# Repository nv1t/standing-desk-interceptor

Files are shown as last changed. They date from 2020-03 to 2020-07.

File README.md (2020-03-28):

# standing-desk-interceptor
I wanted to intercept the communication between my Flexispot E5B standing desk buttons. This is the progress on the project.
It should work on any other flexispot desk as well, as i suspect they use the same button interface with nearly the same protocol. But this needs testing!

# RJ45 Pins
```
1 - RES
2 - SWIM
3 - ?
4 - WAKE
5 - RX
6 - TX
7 - GND
8 - VCC
```

# Using SWIM
The SWIM Debug interface is on the RJ45 Port, but not possible to use, due to set Read Protection, which can only be disabled by overwriting the Chip itself.

# Protocol
Every Command starts with 0x9b and ends with 0x9d. The second byte is the length of the Message with the Endbyte included.

Those are the know commands from the button controller to the motor controller with their respective button names.
```
commands = {
    'reset': '\x9b\x06\x02\x00\x00\x6c\xa1\x9d',
    'Mod2':  '\x9b\x06\x02\x08\x00\xac\xa6\x9d',
    'Mod1':  '\x9b\x06\x02\x04\x00\xac\xa3\x9d',
    'down':  '\x9b\x06\x02\x02\x00\x0c\xa0\x9d',
    'up':    '\x9b\x06\x02\x01\x00\xfc\xa0\x9d'
}
```

Further inspection can be made by intercepting the commands and bit flip to find out where the table height is included.

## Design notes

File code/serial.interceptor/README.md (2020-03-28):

Opens Up two Serial connections on both ends with normal TTL-USB Interfaces (you need two).

It checks in an endless loop if files Mod1/Mod2 exists in ctrl-Directory and doesn't redirect to packages from the button controller, instead writes his own packages to the motor controller interface.

It is a simple way and just testing. Not finaly and not deployable.

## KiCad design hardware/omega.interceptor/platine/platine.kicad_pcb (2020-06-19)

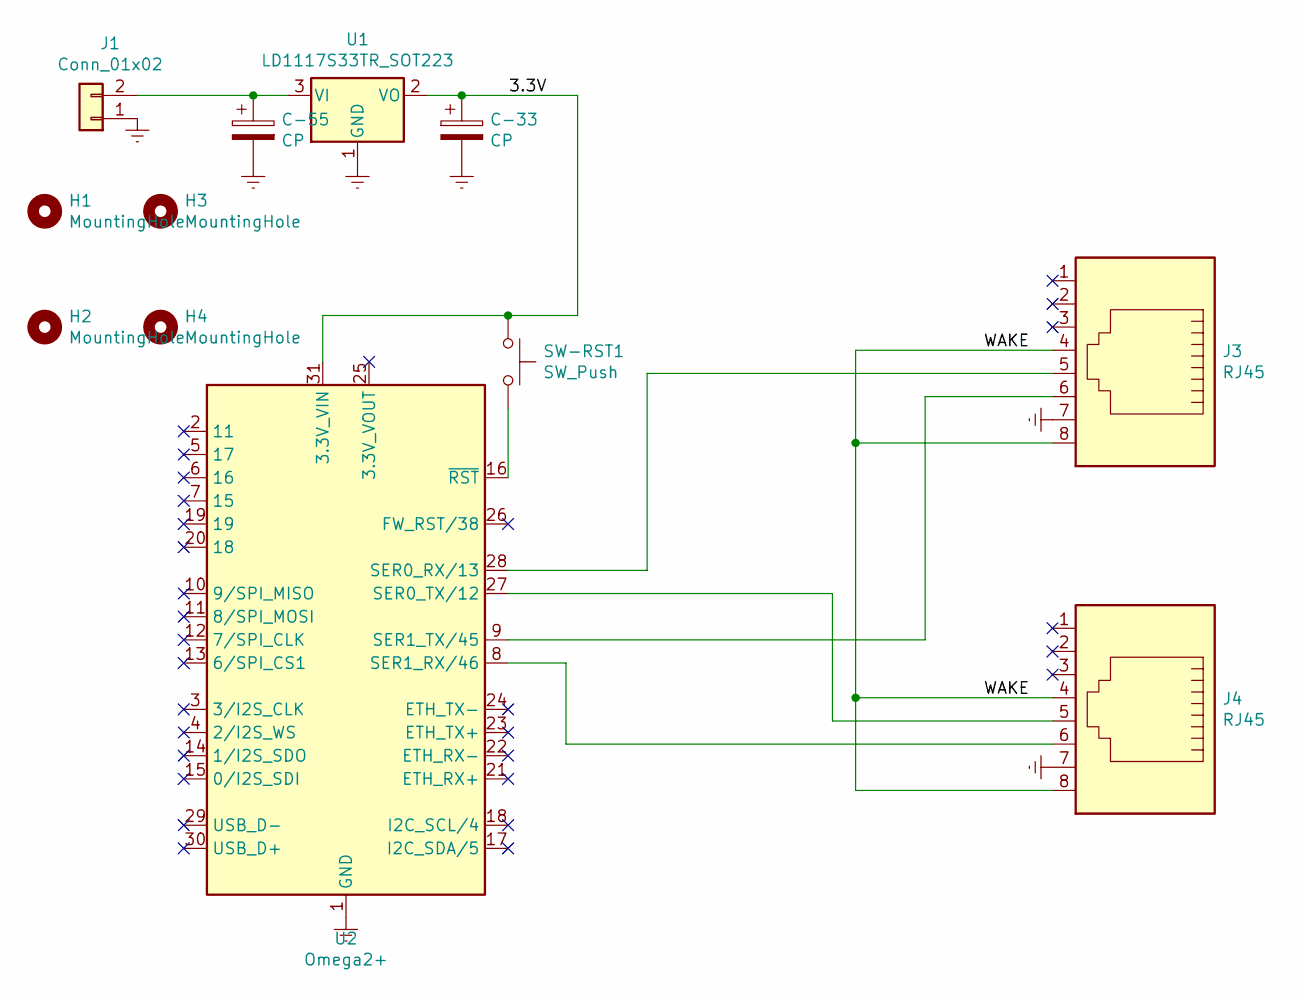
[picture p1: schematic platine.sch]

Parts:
C-33, C-55: CP; CP_Radial_D4.0mm_P2.00mm
H1, H2, H3, H4: MountingHole; MountingHole_2.7mm_M2.5
J1: Conn_01x02; PinHeader_1x02_P2.54mm_Vertical
J3, J4: RJ45; MEBP_8-8G
SW-RST1: SW_Push; SW_DIP_SPSTx01_Slide_6.7x4.1mm_W7.62mm_P2.54mm_LowProfile
U1: LD1117S33TR_SOT223; TO-126-3_Horizontal_TabDown
U2: Omega2+; ONION_OMEGA2

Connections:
/3.3V: C-33.1, SW-RST1.1, U1.2 (VO), U2.31 (3.3V_VIN)
/WAKE: J3.4, J3.8, J4.4, J4.8
Earth: C-33.2, C-55.2, J1.1, J3.7, J4.7, U1.1 (GND), U2.1 (GND), U2.32 (GND)
unnamed: C-55.1, J1.2, U1.3 (VI)
unnamed: J3.5, U2.28 (SER0_RX/13)
unnamed: J3.6, U2.9 (SER1_TX/45)
unnamed: J4.5, U2.27 (SER0_TX/12)
unnamed: J4.6, U2.8 (SER1_RX/46)
unnamed: SW-RST1.2, U2.16 (~RST)

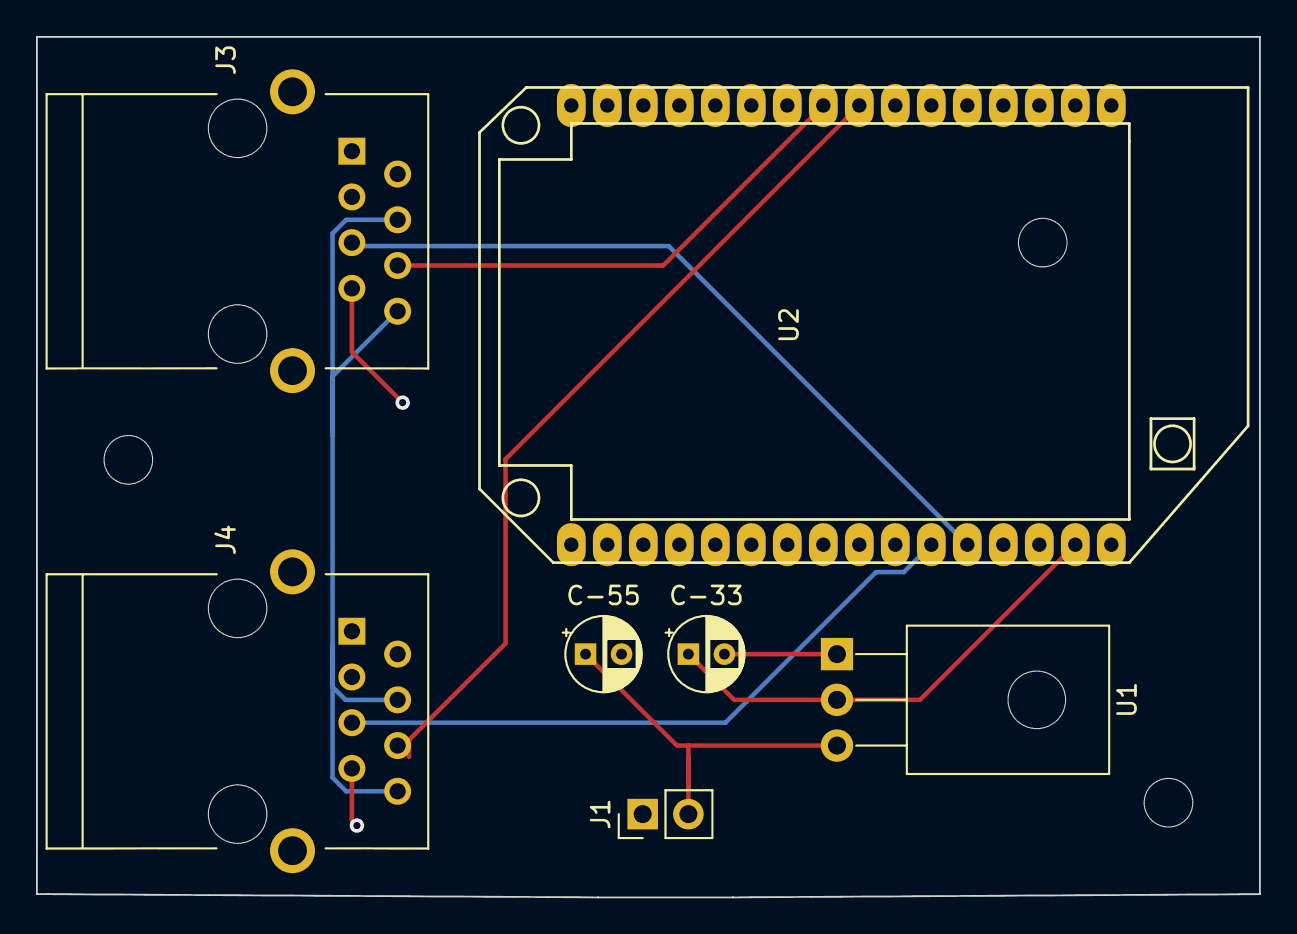
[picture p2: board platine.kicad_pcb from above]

Board: 2 copper layers, 67.9 x 47.8 mm, 11 parts (0 on the bottom side), 8 nets.

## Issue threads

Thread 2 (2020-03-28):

Document Protocol structure

nv1t, 2020-03-28:
This is an ongoing process.
I know the start and endbyte and 1 byte is length.

I know the commands for every button, needs documentation and maybe more interception. wanted to do this with the omega in place for longer data retention and generation of more samples.

nv1t, 2020-03-28:
what i know is document in readme.

Closed 2020-03-28.

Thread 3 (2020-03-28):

using one UART interface

nv1t, 2020-03-28:
It should be possible to use 1 Uart interface and disconnect the transmitt line, if you want to send from your microcontroller.
A friend thought of something: (sorry in germany)

"Also, was wir aus deinen Daten lernen: Wir haben es mit 5V-Logik zu tun. Das heißt, wir brauchen zwischen dem Omega und dem Motor einen Level-Shifter. Die FETs für diesen Level-Shifter können wir aber wahrscheinlich auch dazu nutzen, um zwischen dem originalen Controller und dem Omega umzuschalten.

Wenn du die Verbindung zwischen Controller und Motor trennst, miss mal bitte:
1) Spannung TX vs GND auf Controller-Seite, einmal ohne Kommunikation (aber Controller ist an), und mit Kommunikation
2) Spannung TX vs GND auf Motorseite (also aus Sicht des Motors eigentlich RX) ohne Kommunikation

Aus diesen Werten können wir ableiten, ob der UART-Sender die Leitung sowohl auf High und Low ziehen muss oder nur in eine Richtung, weil die Leitung z.B. durch einen Pullup-Widerstand im Ruhezustand immer High liegt. Letzteres würde den Level-Shifter und das Umschalten vereinfachen, im anderen Fall geht es aber auch.

Für den Level-Shifter am RX-Pin des Omegas reicht ein einfacher Spannungsteiler, z.B. aus 300 und 200 Ohm (ergibt 10 mA Strom bei 5V, das sollte der UART-Treiber am Motor können). "

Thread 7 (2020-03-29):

free ttyS0 on Omega

nv1t, 2020-03-29:
The UART0 Pins on the Omega are used for bootmessages and what not.
You have to disable them, if you want to use both serial consoles.

nv1t, 2020-03-29:
# Disable Boot Serial Console

Disable askconsole in /etc/inittab
```
::sysinit:/etc/init.d/rcS S boot
::shutdown:/etc/init.d/rcS K shutdown
# ::askconsole:/usr/libexec/login.sh
```
# Kernel output Messages
The other default behavior of the Omega that uses the serial port is kernel debug messaging.
Disabling this behavior simply requires that we set the default console_loglevel high enough that no kernel messages will be output on the serial port.

add line to /etc/sysctl.conf
```
kernel.printk=0 4 1 7
```

nv1t, 2022-03-07:
probably not going to use the omega. There are better projects with an esp32

Closed 2022-03-07.

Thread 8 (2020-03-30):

Using 5V from RJ45 to power Omega

nv1t, 2020-03-30:
I want to setup the device inbetween, without adding another powercable.
The RJ45 has a VDD of 5V, the Omega needs 3.3V.

A power regulator LD1117, should be find.

(Source: https://docs.onion.io/omega2-docs/hardware-prep-no-dock.html)

nv1t, 2020-03-30:
Tried setting up an interceptor with a halfed interceptor board (works quite nice) and the omega expansion dock.
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

Problem is: The omega reboots after approx 18-19sec, due to power spike.

The reculator needs two capacitors to `V_in` and `V_out` of the regulator, but don't have them here.

"My recommended spec is input 47uF and output 470uF to handle power inrush demand by Omega2's sudden WiFi power on in around 19-20 seconds into the boot.
Also, do not use thin power supply wires. I recommend minimum of 22 Ga." - (Source: https://community.onion.io/topic/2375/resolved-omega-2-powered-without-dock-shuts-off-after-18s/3)

nv1t, 2020-03-30:
There's an open ticket for it in omega-docs repository.
It looks like they know this issue (since 2017)

https://github.com/OnionIoT/Onion-Docs/issues/51

nv1t, 2020-03-31:
I tried with two capacitors 0.1uF `V_in` and 10uF on `V_out`. Stills drops out. Maybe te capacitors are too small? (only ones i had available, which matched the datasheet)

Have to increase the capacitors to see if the voltage drop is still there.

thinking about opting for the easier solution just powering it from an external usb power device for now and doing a board switch later.
Interestingly i can run it with 5V from external power supply, but not from the rj45 pins. seem to be to unstable.

nv1t, 2020-03-31:
The Board Layout as to accommodate a usb-c or usb-micro for powerrail and possible disconnect between the rj45 and powerrail.
This way, the switch between powering the omega with an external powersupply is much easier and no new layout has to be made.

If the layout works, maybe the usb-c can be dropped in a later stage. (Rev02 maybe)

nv1t, 2021-02-05:
Pulling power from the main line for the Microcontroller results in a error code from the motor controller, because it draws to much power...

fabicodes, 2021-02-05:
How much power does an omega board draw? I've tested it with an ESP8266
which didn't cause any issues

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

nv1t, 2021-02-19:
If you power it directly from the the 5V without the control panel it does work. having the CP in the loop, it faults out for me. i have to recheck with an esp32. I tested it with a RPi Zero, which was way to power hungry.

Closed 2022-03-07.

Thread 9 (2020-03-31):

Using Switch for both RX/TX

nv1t, 2020-03-31:
The RX0/TX0 needs a switch for not intercepting the communication. This way the board can be turned of, if the the communication fails.

The same goes for RX1/TX1. We listen here in Production only anyway. But for intercepting and bit flipping and figuring out the protocol, having an option to intercept the communication would be nice.

RX0/TX0 has to be outside of the board, so it can be used from the outside of the enclosure.

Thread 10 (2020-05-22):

Posibility to use with custom controller based on ESP32

Evghenix, 2020-05-22:
Hello,

Thanks for your work, it's really nice! Good job!

Are you pleanning (if it's possible) to create sort of sdk/api/library (whatever) in order to make possibil to use some custom controllers based on ESP32 or something? It would be really really nice to have.

nv1t, 2020-06-11:
The up and down commands should be possible to use from an esp32 right now :) You just have to set Pin4 to high and talk serial on RX/TX Pins.

I don't know where the height is stored at the moment. Didn't come around designing the pcb for intercepting

Future plan would be having an omega onion to intercept the communication and control the table with both the custom mc and the normal buttons.

But once, the protocol is in the open, it should be easy to implement a custom controller :) it is just normal serial communication, which should be possible with every MC

evghenix, 2020-06-11:
@nv1t Nice job. Please don't stop. This can be a great project. Let me know if I can contribute, I'm frontend software engineer, so I can do web UI, not sure I can do something for this project, but I'll be glad to help.

nv1t, 2021-02-04:
I had a look into the esp32 and i think i am going to use it as a main Microcontroller for this project. It does support 2x UART Interfaces and MicroPython. I have seen some Threading/asyncio implementation and it really might be the right platform for this :)

grssmnn, 2021-02-05:
@evghenix feel free to have a look: https://github.com/grssmnn/ha-flexispot-standing-desk
I still have a problem when the control panel is turned off and I try to query the height. The desk controller is returning `0x00 0x00 0x00` as payload.

evghenix, 2021-03-10:
 @grssmnn @nv1t I've started new project. Currently it's in development phase but MVP is done (probably with some bugs) :)
The goal is to collect as many desks as we can with similar functionality and have sort of universal firmware for them. You can check the homepage https://deskmatik.com and the repo https://github.com/deskmatik/deskmatik

It's written in C++ not sure how bad or good is it, C++ is not mine best skill and it supports Flexidesk (thanks for the protocol interception). Tested it with ESP8266 (NodeMCU)

Now it has WiFi connection interface. It tries to connect to the WiFi network, in case it fails the ESP starts Access Point mode. In this mode you can connect to its WiFi network, navigate to default IP which is 192.168.4.1 and setup your WiFi network credentials. The desk control is now done over simple http requests.

Feature plans:

1. Add more main boards like ESP32 (which is probably already supported, just have to check this).
2. Create good and intuitive UI.
3. Integrate MQTT communication protocol.
3. Make home assistant integration.
4. Native mobile app.
5. More features like Pin Code, scheduled movements to the desired position, etc.
6. Maybe a security protocol implementation even in your local network will be a great plus.
7. OTA updates.

A lot of ideas and not too much free time. Hope you can enjoy the app.

iMicknl, 2021-03-25:
And if you use Home Assisant, I have just built anESPHome implementation: https://github.com/iMicknl/LoctekMotion_IoT/tree/main/packages/esphome. You can use all presets (up to 4 if your device allows it), up/down and it will display the height.
(I have the same issue as @grssmnn here, the height will only be refreshed after you execute a command).

@evghenix looks great! Cool project :)

evghenix, 2021-03-26:
Hey @iMicknl , thanks. Cool project. It looks like more desks are using same communication protocol. BTW, I also started developing the native app for it. I'll updated you when I have first stable release. I'm planing the mobile app as well.

The app will make all stuff user friendly. Currently my app has settings and control views. Also you're able to control the desk using hotkeys. CTRL+ALT+UP, CTRL+ALT+DOWN and CTRL+ALT+1,2,3 to move the desk at saved position.

Here are some screen shots.

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

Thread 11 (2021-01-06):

My findings

fabicodes, 2021-01-06:
Hello,
first of all many thanks for your work so far. I came across your repository by accident, after I got stuck with the height decoding myself.
I have an EK2 table from Flexispot. I haven't decoded the buttons yet, but I'm pretty confident that they are identical to yours.
For the heights, I assume that they are stored in the control unit itself, but that's just a guess.
To record the data I currently have a solution of a RJ45 splitter and a Saleae Logic Analyzer Clone.
Later I want to use an ESP8266 to do the communication with it. I can then also integrate this via MQTT into my home assistant.

Have you made any progress so far, or have you let the project rest since then?

Here is some data that I have found out so far:

Messages between the Controller and the Panel:
```
MSG Control Panel: 	9B 06 02 00 00 6C A1 9D
RESP Motor Control:	9B 04 15 BF C2 9D		9B 04 11 7C C3 9D

MSG Control Panel: 	9B 06 02 00 00 6C A1 9D
RESP Motor Control:	9B 04 15 BF C2 9D		9B 07 12 7F FD 4F 04 A4 9D		9B 04 11 7C C3 9D
```

Some more height data:
```
86.3	9b 07 12 7f fd 4f 04 a4 9d
87.0	9b 07 12 7f 87 3f 80 86 9d
87.3	9b 07 12 7f 87 4f 64 87 9d
87.9	9b 07 12 7f 87 6f bc 86 9d
88.0	9b 07 12 7f ff 3f 80 a4 9d
88.3	9b 07 12 7f ff 4f 64 a5 9d
88.8	9b 07 12 7f ff 7f 70 a5 9d
89.0	9b 07 12 7f ef 3f 40 a9 9d
89.1	9b 07 12 7f ef 06 52 69 9d
89.2	9b 07 12 7f ef 5b ab a8 9d
89.3	9b 07 12 7f ef 4f a4 a8 9d
89.4	9b 07 12 7f ef 66 7a 69 9d
89.5	9b 07 12 7f ef 6d bd 28 9d
89.6	9b 07 12 7f ef 7d 71 29 9d
89.7	9b 07 12 7f ef 07 92 a8 9d
89.8	9b 07 12 7f ef 7f b0 a8 9d
89.9	9b 07 12 7f ef 6f 7c a9 9d
90.0	9b 07 12 6f bf 3f 85 94 9d
90.1	9b 07 12 6f bf 06 97 54 9d
90.2	9b 07 12 6f bf 5b 6e 95 9d
90.3	9b 07 12 6f bf 4f 61 95 9d
```

My current recording setup:
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
My control panel:
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
[The manual of my desk](https://de.flexispot.com/media/productattach/e/k/ek2_montageanleitung_1.pdf)

nv1t, 2021-01-31:
Hi Fabicodes,
Sorry for the reaaally late answer. I have a raspberry pi as intercepting proxy between the motorcontroller and the controlpanel. It is a serial connection, therefore i dropped the logic analyzer from my setup.

I am not sure about the heights. I think i was able to replay a button without the controlpanel attached. That would mean the height is encoded in the command itself. Because the Button commands are fixed, the height has to be stored on the motor controler side.

I haven't looked into the data since the project rested, because i didn't have any time working on it. The project was on hold for quite a while, because of the intercepting proxy...i wanted to build something more stable to use with other projects....and this took quite some time :)

Feel free to push/merge, work on it :) happy not to be alone on this one.

nv1t, 2021-01-31:
ok...i had a look around. somebody worked on it. it is on german: https://www.mikrocontroller.net/topic/493524

nv1t, 2021-02-02:
I have added the height the encoding of the height to the readme file in front.

fabicodes, 2021-02-04:
> ok...i had a look around. somebody worked on it. it is in german, but explains it really really good: https://www.mikrocontroller.net/topic/493524

Whoa, this is an awesome finding! Thank you very much :)

iMicknl, 2021-03-28:
@fabicodes I was wondering if you were able to capture the 'wake up' command to receive the current height. I wrote a ESPHome implementation for Home Assistant, but I only receive the new height when I execute a command like presets / up / down. (or if I wake up the desk controller screen by touching it).

Do you perhaps know if the PIN20 needs to be high/low when you execute the wake up command?

fabicodes, 2021-03-29:
@iMicknl Unfortunately my control panel reacts as immediately as you press a key with the action that the key should perform. Therefore, I doubt that I will find a wake-up command in my control panel variant. But I noticed yesterday by accident at my girlfriend that her controlpanel only wakes up when a key is pressed and displays the height.
I will have a closer look at this soon(™, probably after the exam period) with the Logic Analyzer.
Thanks for the ESP-Home implementation, by the way, that was also on my ToDo list.

Her panel looks like this:
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
(Source: https://de.flexispot.com/elektrisch-hohenverstellbares-gestell-eq5.html)

iMicknl, 2021-03-29:
> @iMicknl Unfortunately my control panel reacts as immediately as you press a key with the action that the key should perform. Therefore, I doubt that I will find a wake-up command in my control panel variant. But I noticed yesterday by accident at my girlfriend that her controlpanel only wakes up when a key is pressed and displays the height.

I feel stupid since I have the same control panel 👀, but indeed you are right.

The 'wake up' command implemented in the [ESPHome implementation](https://github.com/iMicknl/LoctekMotion_IoT/tree/main/packages/esphome) is perhaps already working for the desk of your girlfriend. I would be interested to learn more about above control panel and pinouts by the way, feel free to do a [PR](https://github.com/iMicknl/LoctekMotion_IoT) if you know more.

Closed 2021-02-02.

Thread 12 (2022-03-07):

Glitching stm8 to disable read protection

nv1t, 2022-03-07:
The stm8 can be voltage glitched to jump over bit readout for the SWIM Protection.

This way we can get the firmware to analyze further.

nv1t, 2022-03-09:
https://itooktheredpill.irgendwo.org/2020/stm8-readout-protection/

But i probably use the stacksmashings board. should be lying around here somewhere.

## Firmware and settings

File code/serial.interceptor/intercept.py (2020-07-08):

from threading import Thread
import time
import serial
import sys
import os

# this port address is for the serial tx/rx pins on the GPIO header
SERIAL_PORT_BUT = '/dev/ttyUSB1'
SERIAL_PORT_CTRL = '/dev/ttyUSB0'
# be sure to set this to the same rate used on the Arduino
SERIAL_RATE = 9600

ser_but = serial.Serial(SERIAL_PORT_BUT, SERIAL_RATE)
ser_ctrl = serial.Serial(SERIAL_PORT_CTRL,SERIAL_RATE)

commands = {
    'reset': '\x9b\x06\x02\x00\x00\x6c\xa1\x9d',
    'Mod2':  '\x9b\x06\x02\x08\x00\xac\xa6\x9d',
    'Mod1':  '\x9b\x06\x02\x04\x00\xac\xa3\x9d',
    'down':  '\x9b\x06\x02\x02\x00\x0c\xa0\x9d',
    'up':    '\x9b\x06\x02\x01\x00\xfc\xa0\x9d'
}

def read_serial(handler):
    buf = ''
    while True:
        buf += handler.read(1)
        if buf[-1].encode('hex') == '9d':
            print(buf.encode('hex'))
            return buf

def ctrler():
    while True:
        if os.path.exists('ctrl/kill'):
            sys.exit(0)
        ser_but.write(read_serial(ser_ctrl))

def board():
    while True:
        if os.path.exists('ctrl/Mod2'):
            ser_ctrl.write(commands['Mod2'])
            time.sleep(0.1)
        elif os.path.exists('ctrl/Mod1'):
            ser_ctrl.write(commands['Mod1'])
            time.sleep(0.1)
        elif os.path.exists('ctrl/kill'):
            sys.exit(0)
        else:
            ser_ctrl.write(read_serial(ser_but))

def main():
    t1 = Thread(target = board, args = ())
    t2 = Thread(target = ctrler, args = ())
    t1.start()
    t2.start()

    try:
        while True:
            time.sleep(2)
    except KeyboardInterrupt:
        t1.join()
        t2.join()

if __name__ == "__main__":
    main()

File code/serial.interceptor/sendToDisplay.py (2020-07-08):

import time
import serial
import sys


# this port address is for the serial tx/rx pins on the GPIO header
SERIAL_PORT = '/dev/ttyUSB1'
# be sure to set this to the same rate used on the Arduino
SERIAL_RATE = 9600

def main():
    ser = serial.Serial(SERIAL_PORT, SERIAL_RATE)
    for line in sys.stdin:
        print(line.rstrip())
        ser.write(bytearray.fromhex(line.rstrip()))
        time.sleep(0.2)


if __name__ == "__main__":
    main()

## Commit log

2020-03-28 initial commit with basic files. More will follow in the next few days
    [interceptor.kicad_pcb, interceptor.sch]
2020-03-28 added basic protocol and pin configuration readme
2020-04-02 added a simple omega interceptor schemata.
    [interceptor.kicad_pcb, interceptor.sch, platine.kicad_pcb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]
2020-06-19 Signifikant changes to interceptor hardware layout * removed usb connector * removed switches for interceptor
    made an easy setup to get it manifactured fast and to start testing the protocol
    [platine.kicad_pcb, platine.sch]
2020-07-08 switched usb devices
